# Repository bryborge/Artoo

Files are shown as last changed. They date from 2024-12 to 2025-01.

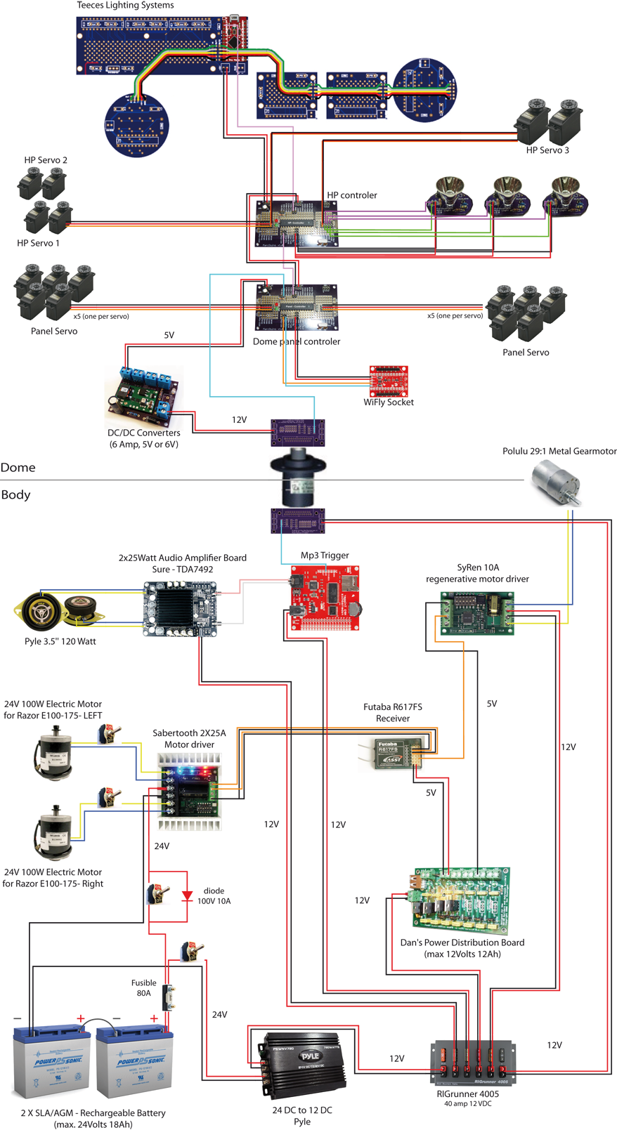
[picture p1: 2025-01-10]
ref/electronics/electronic-schema-24v.png

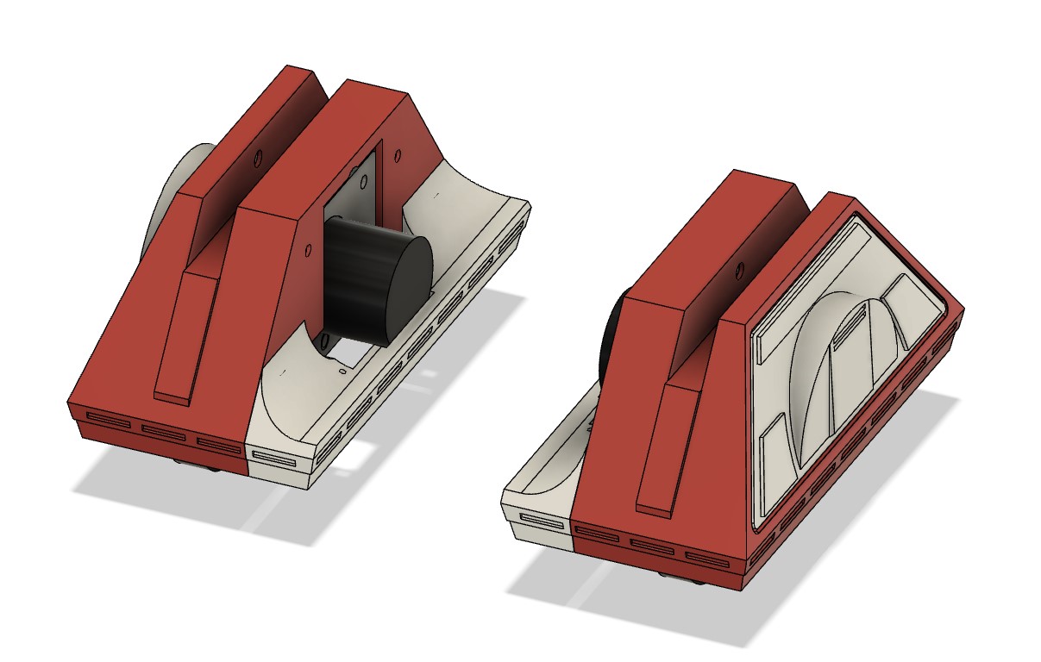
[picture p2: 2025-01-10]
ref/guides/scavenger-drives/Scavenger Drive Foot Covers/Screenshot 2021-05-20 181121.jpg

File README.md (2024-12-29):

# Artoo (Detoo)

Resources, code/sketches, and documentation related to building the Astromech droid R2D2.

## References

### MACs

*   **BT module:** `E8:9C:25:5C:9B:C9`
*   **Foot Controller:** `04:76:6E:85:17:FD`
*   **Dome Controller:** `00:06:F5:B4:F1:E1`

### Further Reading

*   https://github.com/Eebel/SHADOW_MD_EEBEL/blob/master/Shadow_MD_Eebel_Tabbed/a_INIT.ino
*   https://github.com/theFPVgeek/SHADOW/blob/master/Shadow.ino
*   https://www.printed-droid.com/kb/pairing-ps-move-controllers/

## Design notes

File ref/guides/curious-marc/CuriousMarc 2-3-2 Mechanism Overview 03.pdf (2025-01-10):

## “CuriousMarc” 2-3-2 R2-D2 System Overview

Marc Verdiell
Feb. 21, 2011

Foreword
The R2-D2 robot seen in the Star Wars movies has three legs. The legs are in supposedly articulated: the center leg is retractable in the body, while the two outer legs have the ability to pivot around their shoulder articulation.

Thus the robot can be seen in two configurations. In “2-leg” mode, he is standing straight up on its two outer legs with the center leg retracted in the body. In “3-leg” rolling configuration, the center leg is extended and the two back legs are tilted backwards (see Figure 1). In the amateur robot building community, the “2-3-2 capability” refers to the ability of the robot to transition from the 2 legs posture to the 3 legs configuration and back.

The original robots seen in the Star War series actually lacked this capability. In the earlier three Star Wars movies (Episodes IV to VI), where R2-D2 is always an actual robot (in the later movies, he is either an actual robot or a computer graphic generated one), different robots are used for each configuration. The “2-leg” robot is usually not moving, and has space inside for a dwarf actor (Kenny Baker¹

) to sit in and bring him to life by moving the dome and shaking it. You can actually spot two small leg tubes under the body where the dwarf actor can slip his feet.

The 3-legged robots, of which many versions were used, were remote controlled units with fixed legs configuration, the center leg being in fixed extended position and the outer one always leaning back at a fixed 36° angle.

Only one version of the robot, the “pneumatic R2”, had the ability to switch from 2 legs to 3 legs, but not the reverse. This was accomplished by powerful pneumatic actuators. This transition is first seen in a short scene²

of the movie “A New Hope” (Episode IV).

- 1 -

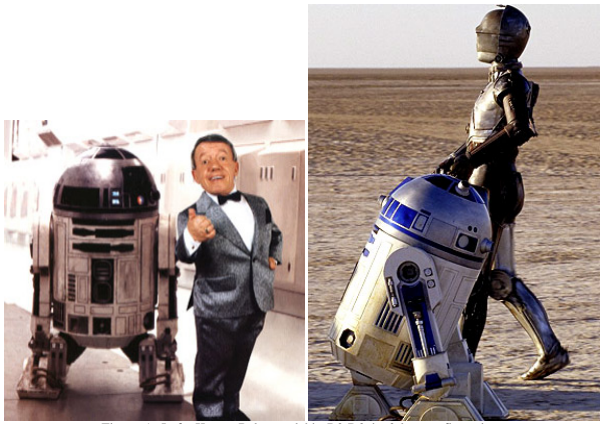
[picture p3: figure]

Figure 1: Left: Kenny Baker and his R2-D2 in 2-leg configuration. Note the tube extensions connecting the underside of the body to the foot shells for the actor’s feet. Right: R2-D2 rolling around in his familiar 3-leg configuration.

Therefore, building an actual 2-3-2 enabled R2-D2 replica goes beyond what the actual movie robots could do, and is generally known as a challenging task for the amateur builder. The difficulties arise not from one particular constraint, but rather from the combination of several of them:
- the limited space available inside the robot, particularly when taking into account the space needed for batteries to operate the robot for long sessions.
- the relatively swift motion necessary to imitate the lifelike 2-3 transition seen in the movie
- the large static and even larger impact forces that the legs and mechanism have to survive once rolling
- synchronizing the movement of the center and outer legs while keeping the robot in balance during the 2-3 and 3-2 transition.
- limited amateur budgets.

Despite these hurdles, several builders have succeeded in building 2-3-2 enabled robots 3, , , , , , , , 4 5 6 7 8 9 10 11. A good discussion of the different approaches used can be found on our builder’s community web forum at astromech.net¹².

- 2 -

This document was put together at the request of one of us (Blake Mann), encouraging all 2-3-2 builders to document their designs to help guiding other builders. It summarizes my own approach to the problem, which owes much to the other builders referenced above. The step by step building progress of my 2-3-2 droid, along with many videos and pictures, is also chronicled on my builder’s log on astromech.net¹³, where I post under my forum moniker “CuriousMarc”.

Shoulder Actuation Mechanism

Figure 2 is a diagram of R2 in 2-leg and 3-leg position. When not standing upright, the angle between the center leg and the outer legs is 36°, which is the amount the shoulder flange on which the outer leg is attached should be rotated by the mechanism.

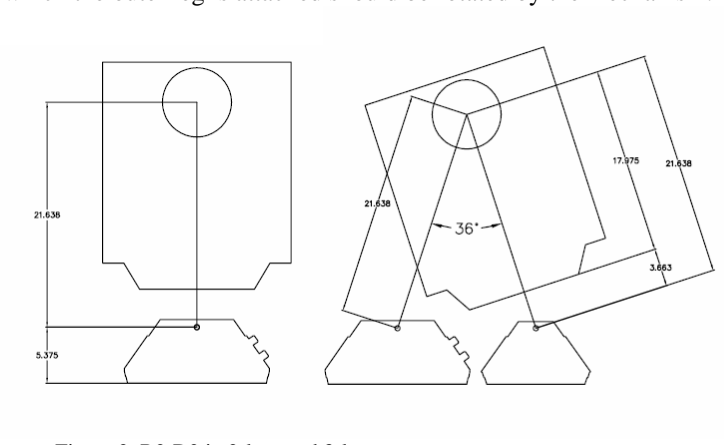
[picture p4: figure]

Figure 2: R2-D2 in 2-legs and 3-legs posture

My shoulder actuation mechanism is shown in Figure 3. It uses a linear actuator instead of the more commonly used, but bulky and fragile, satellite motor arrangement (the “satellite motors” owe their name to their original function, which was to rotate satellite TV dishes).

- 3 -

Figure 3: Views of CuriousMarc’s R2-D2 shoulder actuation mechanism

My R2 is based on the COM-8 frame, made by James Van Reenen (see Figure 4). My COM-8 Frame model is a modified version of the JAG 5 frame originally developed by Jerry Greene. The COM-8 plans are not publicly available, but the dimensions follow the Jerry Greene plans very closely, which are available on his web site 14. I adapted my mechanism to fit the existing frame with little or no modifications. Indeed, one need to drill only two ¼” holes in the COM-8 shoulder plate to accommodate my shoulder mechanism.

- 4 -

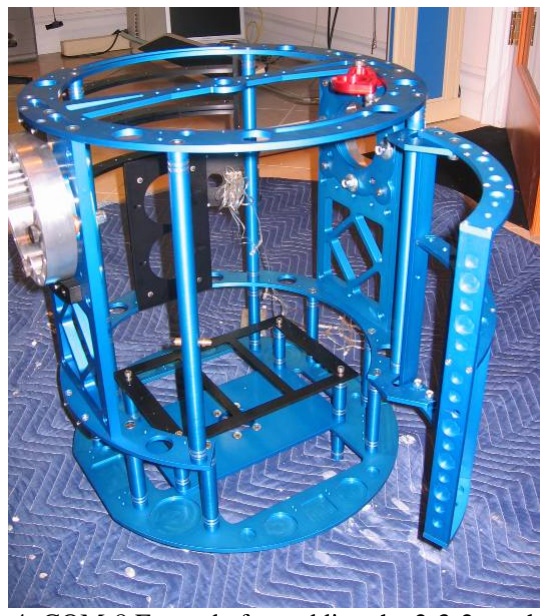
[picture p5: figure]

Figure 4: COM-8 Frame before adding the 2-3-2 mechanism.

The COM-8 shoulder mounting plate is shown in Figure 5. Like the one on the JAG-5 frame, it incorporates 4 curved races that allow for the shoulder flange to rotate through the necessary range. The frame also comes with bronze bushings that slide into the curved openings, so a fair amount of 2-3-2 readiness is already built into the frame.

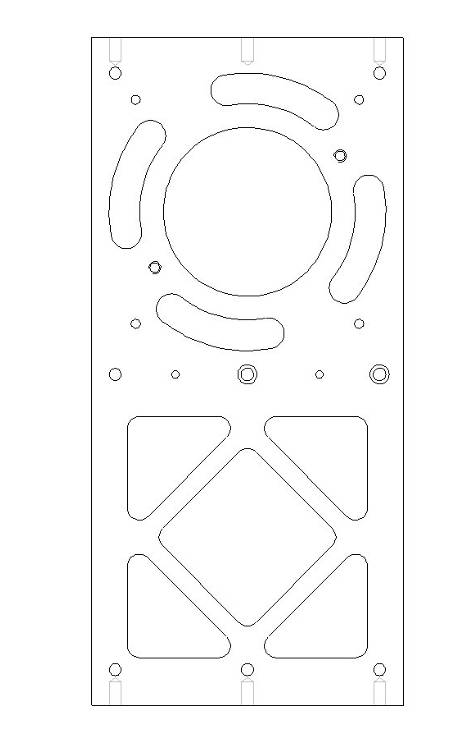
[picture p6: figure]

Figure 5: Shoulder mounting plate that comes with the COM-8 frame, showing the 4 curved 48°openings.

The actual races allow for 48° of movement, 38° in the backward direction (2° more than needed for 3-leg position) and an extra 10° forward, so R2 can actually look down when

- 5 -standing in 2-leg position. My mechanism supports the full range of motion, both backward and forward.

The first task was to size the actuator. Initial calculations showed that two 100 lbs actuator with a 3” stroke would easily cope with a 150 lbs robot, 48° rotation, and a 1 to 2s rotation time using a relatively short lever arm compatible with the available physical space around the shoulder. I chose a 100 lbs semi-custom unit from Motion System¹⁵, model 85615 16 (see Figure 6). This unit has several advantages. It is very compact and fits behind the shoulder plate, is available in 12V drive, has very fast movement (available either 1”/s or 2”/s, I used the slower 1”/s model). Most importantly, it has a recirculating ball screw which allows it to free-wheel at both travel ends, eliminating the risk of mechanical damage.

There are a boat load of options that need to be specified when ordering the actuators, and the final part numbers are 85615-LH-15-3-SBC-0.250-DC1-RE-CT and 85615-RH-15-3-SBC-0.250-DC1-RE-CT. They also became more prosaically known as the “85615 R2-D2” RH and LH actuators (units are not symmetric, you need a right handed and left handed one), I suspect you can re-order them using that simplified code.

The actuator connects at the bottom with a small anchor that I machined, and at the top to a J-bar, as shown on Figure 7. The J-bar connects to the original COM-8 shoulder screws, with the simple addition of slippery Rulon and Nylon thrust washers sandwiched between the bar and the shoulder plate. The J-bar dimensions are given in Figure 8, and are intended to give full 48° range of motion with a 3.0” stroke from the actuator.

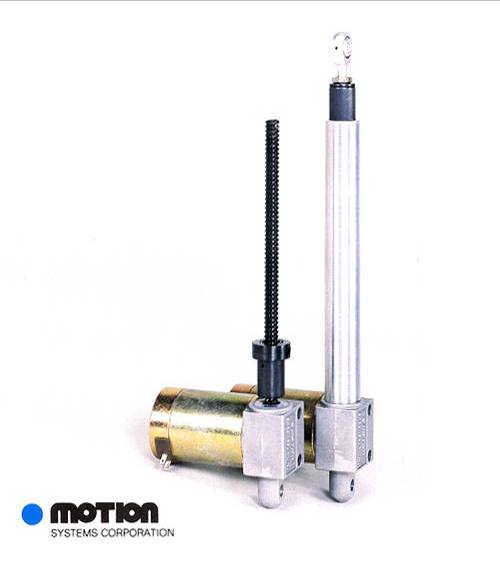
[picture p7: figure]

Figure 6: Linear Ball Drive Actuator model 85615 from Motion System Corp.

- 6 -

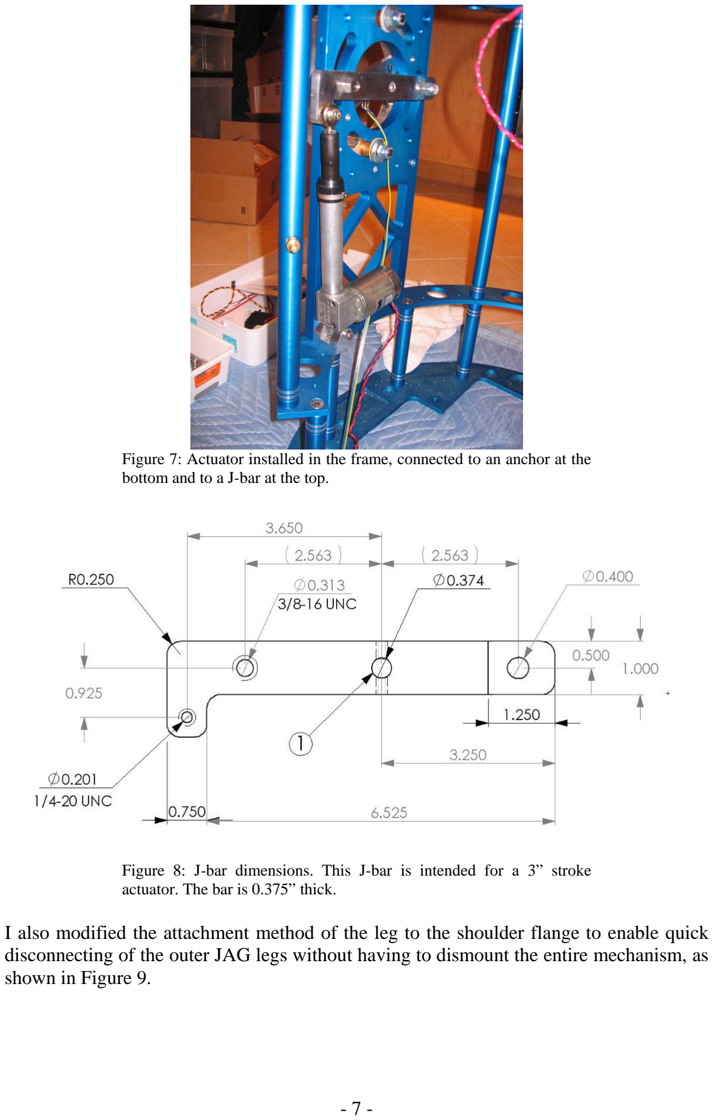
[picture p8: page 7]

Figure 7: Actuator installed in the frame, connected to an anchor at the bottom and to a J-bar at the top.

Figure 8: J-bar dimensions. This J-bar is intended for a 3” stroke actuator. The bar is 0.375” thick.

I also modified the attachment method of the leg to the shoulder flange to enable quick disconnecting of the outer JAG legs without having to dismount the entire mechanism, as shown in Figure 9.

- 7 -

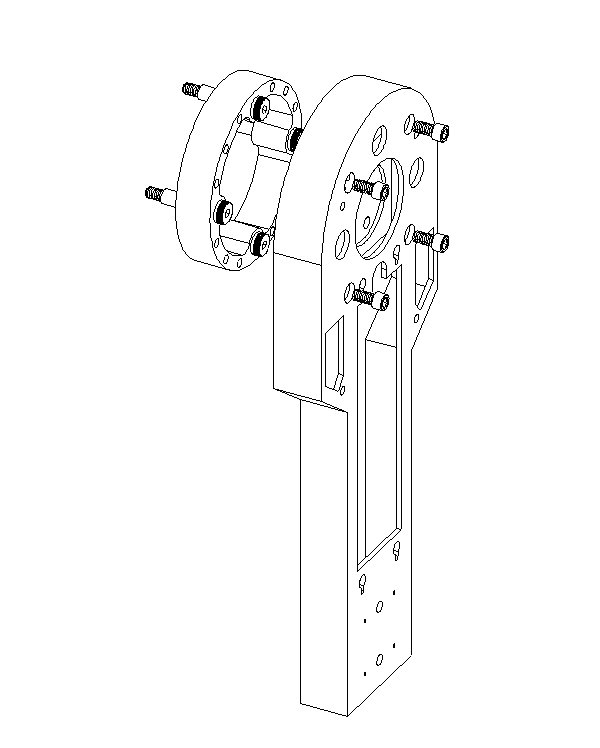
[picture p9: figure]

Figure 9: Modified leg to flange assembly.

Outer Leg servo control

I control the outer leg position in a continuous and analog fashion like a regular servo. I used a linear 10kΩ potentiometer as a position sensor. When connected to a motor controller having feedback capability, this effectively transforms the leg actuator into a giant servo. This way, no limit switches are necessary, and the 2-leg, 3-leg and lookdown positions can be adjusted using the RC transmitter programming, or software in the 2-3-2 motion controller as I describe later on. Also, all intermediate positions of the leg can be accessed.

A spanner was designed to fit inside the shoulder flange opening and hold the position sensing potentiometer, as well as a mounting pin for the ankle angle control bar to be discussed below. The spanner mounts on the outside of the shoulder plate using the two aforementioned ¼” holes drilled in the plate. Drilling these holes is the only modification necessary to the COM-8 hardware. The spanner is shown in Figure 10.

For the servo motor control, I used a RoboteQ AX500 dual 2x15A controller¹⁷. To be fair, this is a bit of an overkill, as the motors do not consume more that 2A and I do not use any of the advanced features. Simpler units from Polulu (use units with position feedback) might be a more economical fit¹⁸.

- 8 -

Figure 10: Spanner with the potentiometer and anchor pin attached (left), spanner mounted on the outside of the shoulder plate (right).

Outer Ankle Locking
One of the trickiest aspect of the 2-3-2 mechanism is the locking of the ankle pivots. The foot shell normally connect to the leg ankle at a pivot point, and is left free to rotate around that articulation. However, the outer ankle-to-foot pivots need to be rigidly locked in 2-leg position so the droid doesn’t fall over. But, in 3-leg mode, the foot shell needs to be at 18° from the horizontal, bisecting the 36° angle of the leg to the body (see Figure 2). Strictly speaking, the outer ankles do not need to be locked at a specific angle in 3-leg position and could be left free. However, builders prefer the added stability and traction provided by locked ankles when driving. Also, reverting from free ankles to locked ankles during the 3-2 transition is a tricky balancing and timing business.

I therefore opted for a simple passive ankle control mechanism, which I believe was first documented in the Carr-Hunger droid. In this implementation, the angle between foot and ankle is maintained at exactly half of the angle of the body to leg at all times via a steel rod, mechanically tying the leg-to-shoulder angle to the foot-to-leg angle.

A few pictures should clarify how this works. A narrow steel bar extends through the whole length of the leg as seen in Figure 11. It goes through a small opening at the bottom of the ankle and is tied to an anchor screw in the foot shell near the pivot point, as shown in Figure 12. The top of the tie rod is attached to a pin near the shoulder pivot point (Figure 13). I have used both stock steel pins (the one in Figure 10) and machined brass pins (see close up in Figure 14) with equally good results. The steel pin is easy to procure, but needs to be force fitted into the spanner, while the machined pin is simply screwed in, but you need to machine it. Choose your own evil…

The trick to maintaining the correct half-angle relationship is to locate the tie point in the foot twice as far from the pivot point as the tie point at the shoulder. In my case, the shoulder pin is ¾” from the center of rotation of the shoulder, while the foot shell tying screw is 1½” from the ankle pivot point, satisfying the needed geometric relationship.

- 9 -

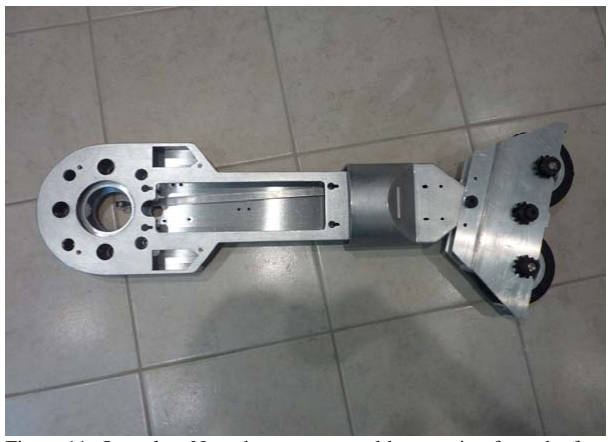
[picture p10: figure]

Figure 11: Outer leg. Note the narrow steel bar running from the foot to the shoulder opening and used for foot angle locking.

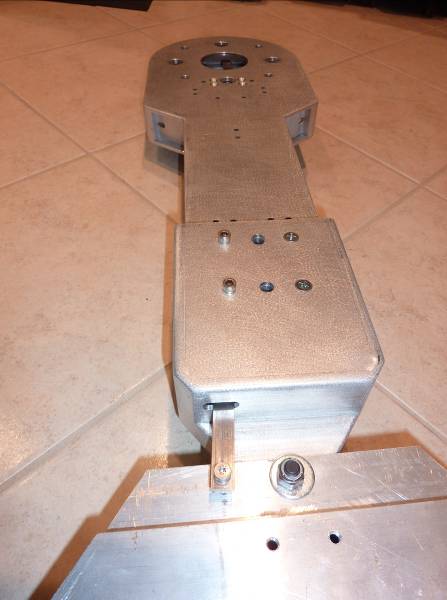
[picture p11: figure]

Figure 12: Lower portion of the outer leg. The ankle tie rod goes through a small opening at the bottom of the ankle and is attached to an anchor screw on the foot shell.

- 10 -

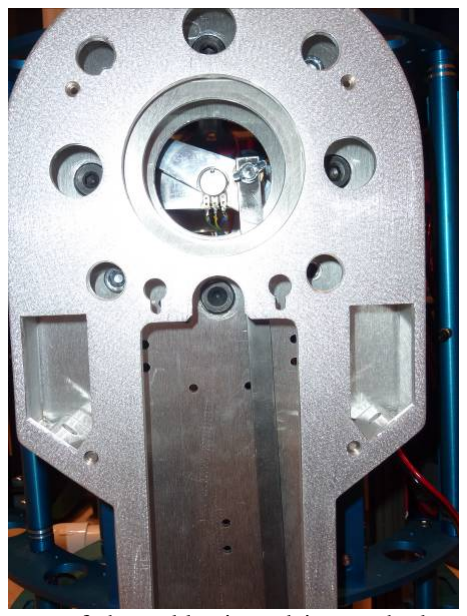
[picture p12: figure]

Figure 13: The top of the ankle tie rod is attached to a pin near the shoulder center of rotation.

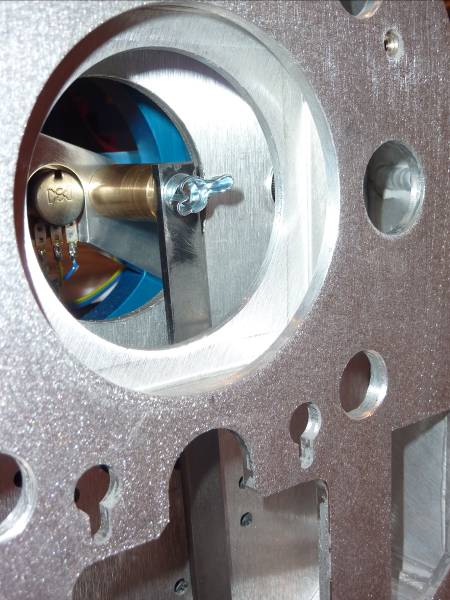
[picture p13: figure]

Figure 14: Detail of the top attachment pin for the tie rod.
Center Leg Lift Mechanism
The center leg lift mechanism was a real head scratcher. One of the best fully documented mechanism I had seen was Mike Lambert’s foot lift, whose plans are available on the Yahoo R2-builders group file section 19. However I did not like the space it consumed at the top of the droid, nor the speed at which it operated. I wanted my foot to drop in a second or two to be more lifelike.

Problem is, when the foot is retracted in the droid body, there is very little space left for a mechanism except towards the top of the body. The mechanism needs a relatively long stroke of 10”. And it has to be extra strong because the center leg has to survive shock

- 11 -impacts many times the weight of the droid from a sudden impact on the front wheels while driving and, unlike the outer legs, these strong forces are right in line with the movement one wants to achieve. Which means such mechanisms are usually large and slow.

After trying many zany configurations that either didn’t provide the speed, the necessary travel length, the strength or the space savings, I finally arrived at a workable solution shown in Figure 15. This self-contained mechanism is also designed to fit into the COM-8 frame with very little modifications, needing just 3 pairs of extra holes on the bottom ring to attach the support brackets.

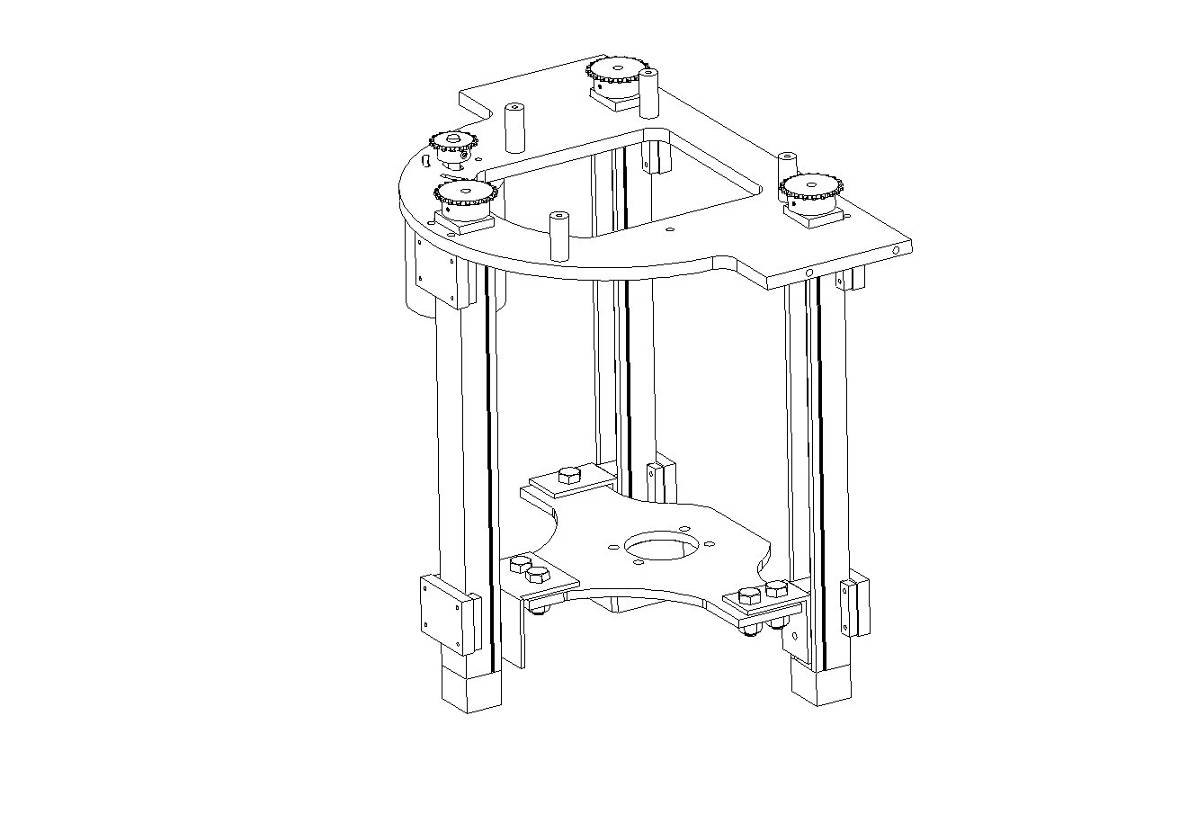
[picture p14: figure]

Figure 15: Center leg lift mechanism

Three screw-actuated linear slides assemblies are the key of the design. The ones I use are manufactured by PBC Linear²⁰. These extruded aluminum units are relatively low cost actuators (that is, relative to most professional linear motion equipment!), very compact, yet have enough structural strength for our application. They can be ordered semi-custom in any length, with several choices of screw pitch. A shown in Figure 16, they are relatively simple units. A slider moves along in an extruded aluminum shell when turning the lead screw. The exact part number for the PBC slide is MLD028D-0AJ201-0338-000 (28x338 mm actuator, 10 mm lead screw).

- 12 -

Figure 16: PCB Linear MLD actuator, part number MLD028D-0AJ201-0338-000. It has a 338mm main body length and a 10 mm lead screw.

One would be tempted to use only one of these slides. However, although they are acceptable (while not spectacular) in axial load performance, they are pretty poor in moment load. They would fail if a large force would tend to twist and rotate the slider. Unfortunately there would be plenty of that if only one of the units was attached to a side of the platform holding the leg. To go around that problem, I use three slides attached around the moving platform. They are all driven in unison by a chain and sprocket system, so that the platform always stays flat and no large moment force can ever develop. A quick calculation showed that the load of a 150 lbs robot including impact load was acceptable, albeit without much margin. Drive carefully as they say.

Next was the issue of travel. A full 10” of travel is needed to barely fit the leg inside the body. Add 0.30” of margin for over-travel at either end, the slider length and the length of the end cap of the units, and quite miraculously the unit barely fits inside the body without going above shoulder level. Beware that the slides protrude all the way down into the skirt, so resin skirts with thick solid sides are out.

Finally, there was the issue of torque and speed. Given the maximum 3,000 rpm critical speed of the screw, there are several combinations of lead screw pitch and drive speed that can achieve the desired 10”/s speed. I chose a 10mm lead screw, which yields a 1500 rpm actuation for the 10”/s speed goal. This would allow up to 2:1 gear reduction to increase torque from typical brushed electrical motors that run in the 2000-3000 rpm regime. Assuming this reduction and a 15 lbs leg weight, calculations showed that a motor with at least 50 oz/in torque and 40W would be needed. A cheap surplus 100W, 12V, 2500 rpm (no load) scooter motor fits the bill with good margin and is small enough to fit underneath the mechanism. The final gear ratio I used was 15 teeth on the motor and 20 teeth on the actuators. I used a #25 chain. The scooter motor has no trouble at all with my heavy center foot and achieved the calculated speed. My only complaint is that it is a bit noisy.

Figure 17 shows the parts needed to assemble the leg lift. They are the top platform and the sliding plate, and a bunch of mounting brackets. They would probably be difficult to replicate without having some machining tools, but could easily be made in a machine shop run. Figure 18 and Figure 19 show the completed assembly in the droid frame.

- 13 -

Pictures do not do much justice to the “life” a quick leg drop brings to the transition, however you can get a better idea from a YouTube video I posted at http://www.youtube.com/watch?v=v9vhstzh6Ok , which is also available along with a few more in my build log.

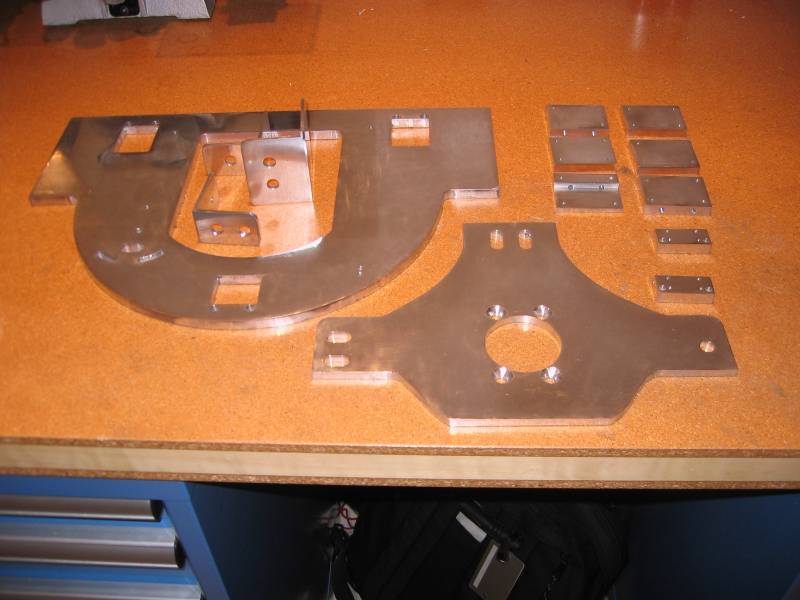
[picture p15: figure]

Figure 17: Aluminum pieces needed for the leg lift.

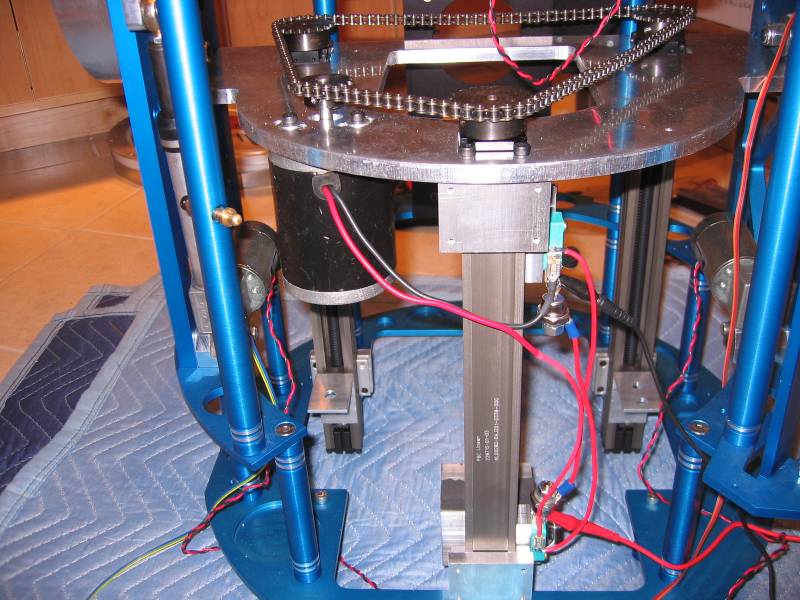
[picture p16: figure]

Figure 18: View of the leg lift mechanism during assembly.

- 14 -

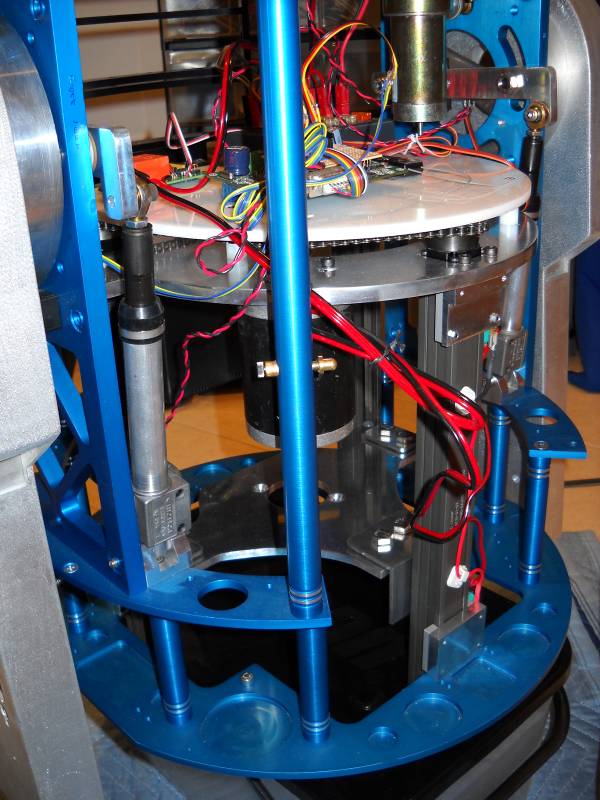
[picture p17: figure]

Figure 19: Completed Leg Lift mechanism.

Center Foot servo control
I used a simple RC dual relay board to actuate the center foot up or down from and RC signal. I bought mine from robotmarketplace.com²¹ (Figure 20). The end travel is controlled by simple micro-switches in either direction, shunted by power diodes to allow reverse movement once the end travel is reached. One could also use a RC brush motor controller and gain some speed control, and maybe I’ll upgrade to that when I get the time. Just be sure to size your relays or speed controller appropriately, the motor can draw up to 10A at full tilt.

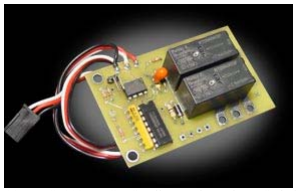
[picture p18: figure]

Figure 20: RCE220 RC Small Dual Relay Switch from robotmarketplace.com

- 15 -

One issue I had with the simple limit switch setup is that since the leg moves very fast and is heavy, cutting the motor supply was not enough to stop the movement. The assembly would travel past the limit switches and bump into the mechanical stops at both ends. In order to decelerate the foot more efficiently at the end of travel, I also use the motor as an electric brake by shunting it. I was able to accomplish this automatically by adding two more (powerful!) shunting diodes to the system as shown schematically in Figure 21.

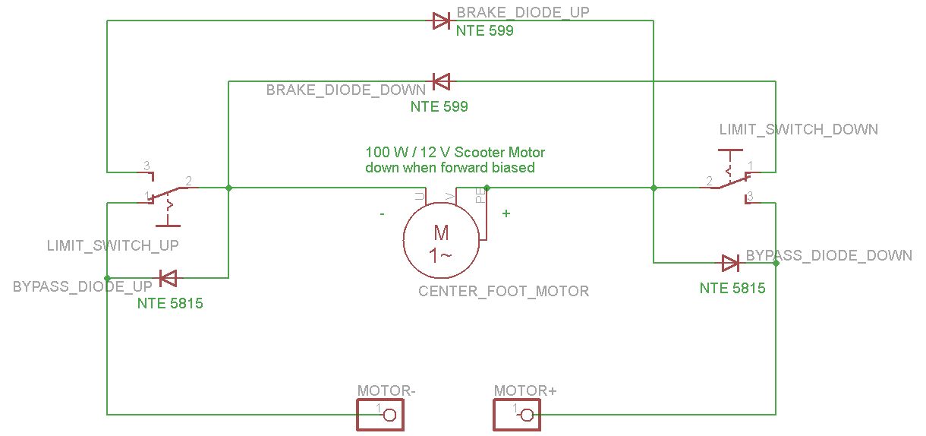
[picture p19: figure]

Figure 21: Limit switches and diodes for the end travel control. The two large NTE599 15A cont / 250A max diodes are for braking at travel end.

The diodes have to be of the larger kind, I use NTE5815 (Io 6A, Imax 400A) over the end switches and two NTE955 (Io 15A, Imax 250A) on a heatsink as the breaking diodes.

Center Foot considerations

I used a two caster setup for my center foot. By using two casters, the center ankle articulation is left unlocked, and the foot naturally adjust to the required angle, which continually varies during the 2-3-2 transitions. The largest caster I could fit is a 3” caster from Mitsumi²². Another builder (TinyP²³) discovered them, they are the only ones whose swivel radius is small enough for two casters to fit in the foot shell without interfering with each other or with the shell skirt when turning around.

One must be careful to introduce some kind of shock absorption device between the actuation mechanism and the center foot wheels, or all shocks would be transmitted directly to the screw actuators. The heavy Mitsumi steel casters are designed for very heavy loads (which is probably why the swivel radius was kept so small), and therefore come with very hard wheels. To provide some shock absorption, I replaced the wheels with soft neoprene wheel from another 3” caster (Figure 22). To provide further shock

- 16 -absorption, I added rubber absorbers (vibration mounts) between the caster plate and the foot shell (Figure 23).

Figure 22: Misumi casters, with the original hard wheel at right, and grafted with a soft neoprene wheel at left

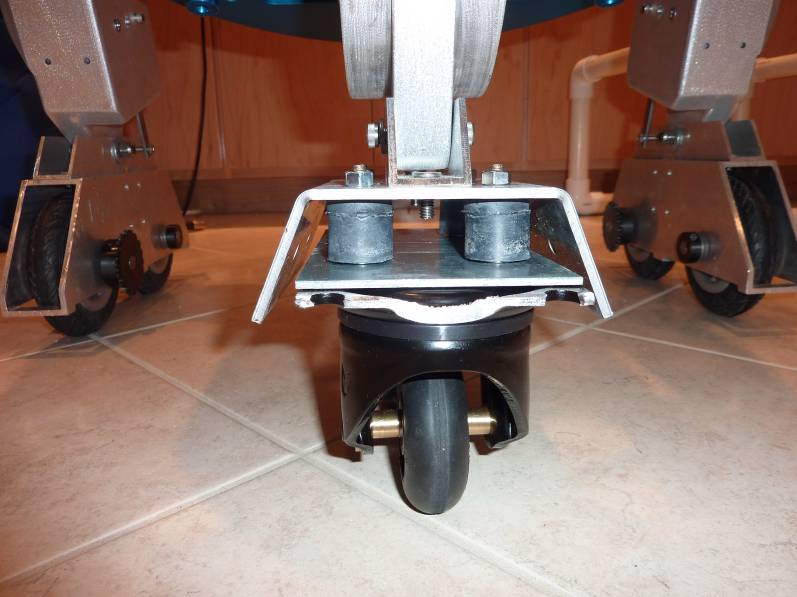
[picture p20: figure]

Figure 23: Rubber mounts are inserted between the caster place and the foot shell for shock absorption.

2-3-2 Motion Controller
With the simple system described above, I was able to do manual 2-3-2 transitions right from my RC controller without further ado. I controlled the outer leg servo with my flap lever, and the center leg via a 3 position switch. However, one has to be careful to first
- 17 -lower the center leg, then move the legs – and the reverse for the 3-2 transition. Do that in the wrong order and the droid will do the dreaded “face plant”.

Most 2-3-2 builders add some form of a controller to synchronize the outer leg and center foot movements for the transitions. I chose to implement this function via a microcontroller, which I can program to output the correct servo signals to feed my three leg servo controllers (two outer legs proportional servo control, and the center leg up/off/down control). It’s a significant programming investment to implement it, but once it’s done it becomes extremely flexible, since all optimizations can be done via software.

The basic system architecture is shown in Figure 24. The microcontroller reads 3 channels from the RC receiver (outer leg channel, center leg channel, and failsafe channel) and 1 analog channel (position sensor of the left outer leg). It outputs 3 servo channels, one for each outer leg and one for the center leg.

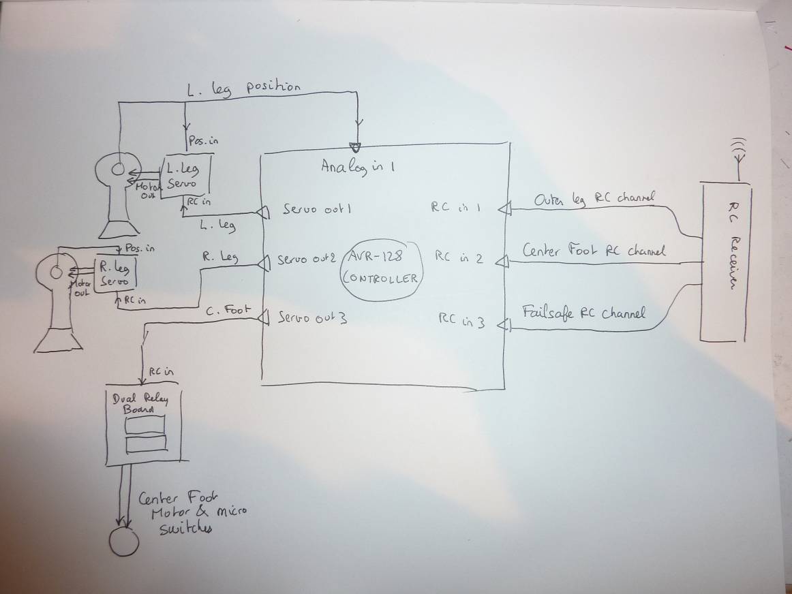
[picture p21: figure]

Figure 24: 2-3-2 control architecture

I used a small and inexpensive Olimex development board powered by an 8-bit Atmel AVR ATmega128 microcontroller²⁴ depicted in Figure 25. In essence it’s very much like an Arduino with a small keypad and LCD screen and a more powerful processor. The amount of microcontroller hardware you get nowadays for about $50 is just downright mind-boggling. This little controller has a 16 MIPS RISC processor, EEPROM, RAM, Flash Memory, 4 independent timers, a real time clock, two independent serial interfaces with support for RS232 and I2C, a whole bunch of PWM generators, 53 pins

- 18 -programmable for input or output, 8 ADC inputs, 8 external interrupts, brownout protection, 6 sleep modes, a bootloader section, in-situ programming, JTAG debug… The list just goes on and on, and so does the 386 pages long manual! And, let’s not forget, unlike PC processors, power consumption is just about negligible. It’s a robot maker paradise or hell, depending on your love of hard core C programming.

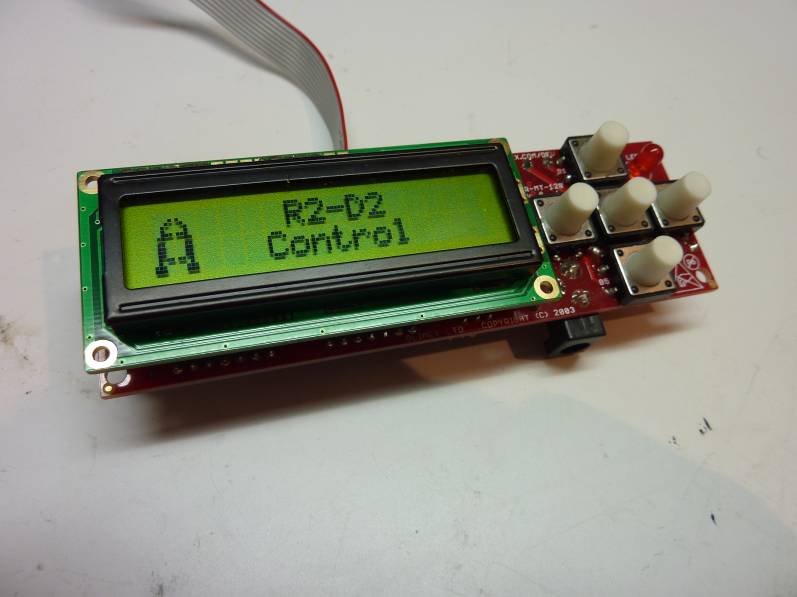
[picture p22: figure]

Figure 25: Olimex AVR-MT-128 microcontoller board

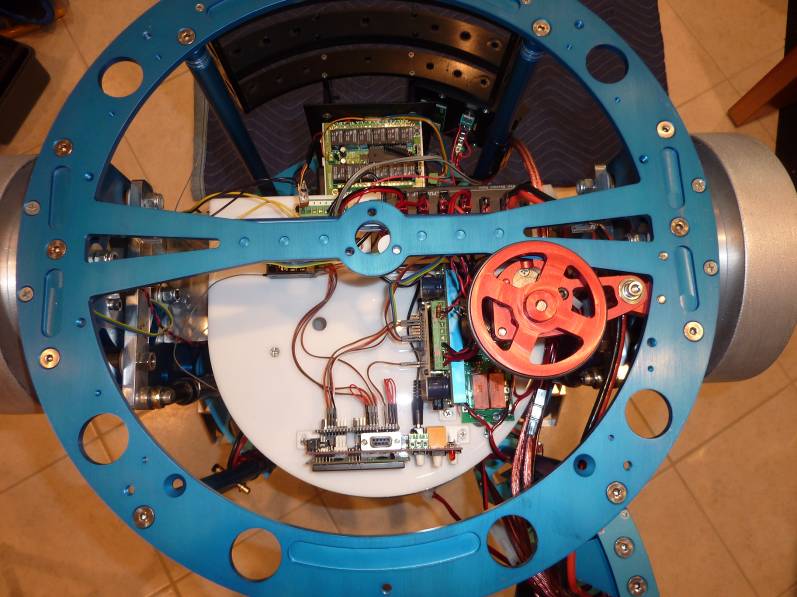
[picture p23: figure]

Figure 26: View of the installed electronics. Controller is at the bottom, to the right is the outer leg servo controller. The relay board for the center foot is partially visible under the dome wheel.

- 19 -

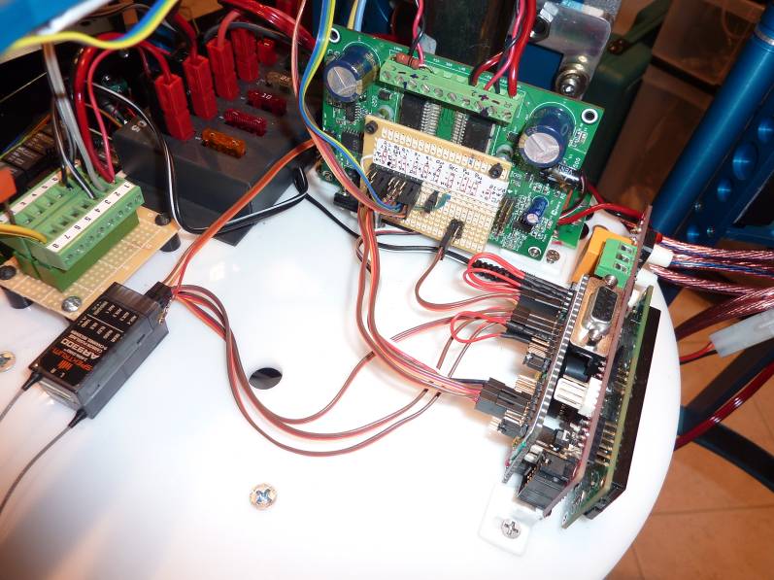
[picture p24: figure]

Figure 27: Close-up view of the electronics. RC receiver to the left, outer leg servo controller to the top, microcontroller to the right.

Figure 28: Controller display in auto mode. The outer legs have been commanded in 2-leg position, as indicated by the close to 500 µs leg channel value read from the RC transmitter. Accordingly, the center leg has been brought to up (U) position. A cumulative run-time counter is at the lower left – R2 has been up for less than a minute and still shows 00:00.

In regular auto mode, the controller simply monitors the outer leg lever position from the RC transmitter. Starting from 2-position, the first little bit of lever position does nothing, then past a certain point the center leg deploys, and the outer leg follows the position of the lever. The outer legs can be moved all the way to full back 3-leg position, or can be brought to any intermediary position using the lever. If the controller senses that the outer legs are brought back all the way upright to 2-leg position, it automatically raises the

- 20 -center leg. While this happens, some basic info is available on the LCD screen for monitoring (Figure 28).

Note that for safety, the controller also monitors an extra “failsafe” channel. If this channel has no signal, goes into a predetermined failsafe state due to a loss of signal at the receiver, or is manually set by a switch on the RC transmitter, all 2-3-2 leg movement is disabled.

In addition to the auto mode, the controller also supports a direct RC mode, a manual mode, a calibration mode and a diagnostic mode. In RC mode, the controller simply passes the RC signals from the transmitter to the outer and center leg, in essence reverting back to my earlier manual control setup. In manual mode, legs can be activated locally at the robot using the controller keypad. The calibration mode is used to set the 2 leg and 3 leg position, even out the two outer legs via software in case there is a small angular difference between them, and set the points at which the 2-3 and 3-2 transitions occurs. Finally, in diagnostic mode, numerical values read for each RC channel (I can read up to 6 of them), each servo output value (also 6), and each analog input (4 of them) are displayed for diagnostic purposes.
Power system
Even with a relatively compact system, battery space is quite limited in a 2-3-2. To save space and weight, I have been using Lithium-Polymer batteries instead of the standard lead-acid ones. The Lithium-Polymer units have 5 times the energy density of lead-acid batteries. I used three 10Ah/14.8V packs²⁵ connected in parallel, for an equivalent capacity of 30 Ah. The batteries are small enough to fit in the back door (Figure 29).

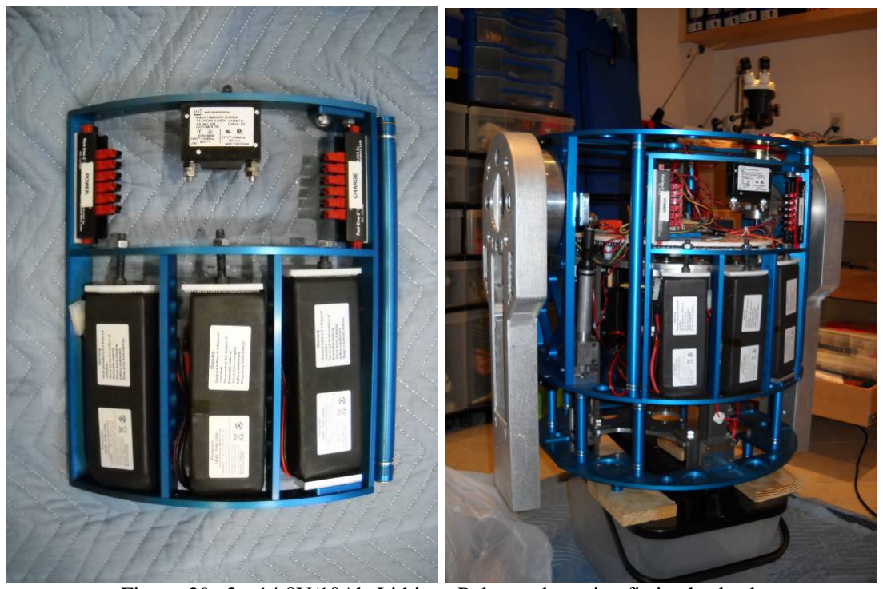
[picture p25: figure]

Figure 29: 3x 14.8V/10Ah Lithium Polymer batteries fit in the back door.

- 21 -

However in actual use I found that the droid was balanced too far to the back – which helps the 2-3 transition, but unfortunately makes driving on 2 legs a bit iffy. The droid would be susceptible to falling backwards when accelerating. I therefore later moved one of the batteries to the front for balance. Fortunately they are so small that you can fit them pretty much anywhere.
Closing Remarks
Figure 30 shows the finished installation. Completion of my 2-3-2 system is recent, so I do not have much extended data on actual use, but it has performed well right from the get go.

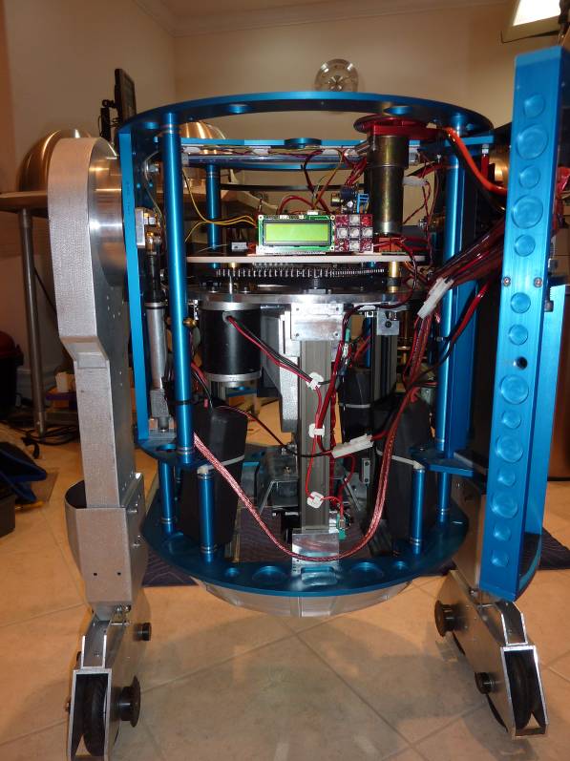
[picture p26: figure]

Figure 30: Finished 2-3-2 installation. Note the batteries in temporary position for balance trials. Eventually I settled on two batteries in the back door and one in the front.

There are a few things I’d change if I was going to make revision 2. The 10mm pitch screw for the center foot elevator is probably a bit too much. The center leg has a slight tendency to retract under the weight of the robot. I eliminated that by introducing a little bit of friction with a belt on the side of the motor shaft, but this is an afterthought kludge in an otherwise clean design. If I had to redo it, I would probably use a 5mm screw instead and compensate for speed with less of a gear reduction.

It is also conservatively designed and expensive. To cost reduce version 2, I would use only one shoulder actuator instead of two, and simply connect the two legs via the classic gas pipe. It would save one actuator and one motor controller cost. Also, now that the three screw system has been proven to work, I would not use pre-made slide assemblies

- 22 -whose precision widely exceeds what we actually need. Instead I would just use regular lead screws, nuts and a few ball bearings and build them into my own mechanism.

Another thing one could do is lighten the frame. Everything gets simpler and more reliable when weight is lower. Since all the weight of the center leg is now transmitted to the top plate of the center foot lift mechanism, the frame itself really does not have to support any weight. Also the horizontal plate greatly reinforces the frame, as do the three vertical slide units. I have effectively built a stronger inner frame inside the original frame. Consequently, the original frame, which is quite heavy, does not need to provide much structural strength anymore. It could be made much lighter without compromising the robot structural integrity.

We have reached the conclusion of this article, however we are at page 23 of what is after all just a quick overview. This should serve as a stern reminder of the significant complexity and challenges that a 2-3-2 system adds to a build. It can be done, and I hope this write-up encourages other builders to take the plunge, but it is definitely not for the faint of heart nor the faint of budget.

- 23 -

References

1
Kenny Baker’s bio: http://en.wikipedia.org/wiki/Kenny_Baker

2
2-3 transition clip from the original movie: http://www.mikeverta.com/Posts/2-3-2.mov

3 Carr-Hunger 2-3-2: http://www.alexkung1.com/r2d2/47/page_01.htm

4
Craig Smith 2-3-3 video: http://www.youtube.com/user/bomarmonk#p/u/9/dSCcJg1n93Y

5
Rob Meyer's 2-3-2 build thread: http://astromech.net/forums/showthre...ght=successful (http://astromech.net/forums/showthread.php?t=2742&highlight=successful)

6 Blake Mann linear actuator demo
http://astromechbuilder.com/mechload...uator.MPG.html (http://astromechbuilder.com/mechloader/v/BMann/2-3-2+linear+actuator/Linear+Actuator.MPG.html)

7
Bob Ross 2-3-2 video at Celebration V: http://www.youtube.com/watch?v=zDn9FnT6buo

8 Cory Paccione 2-3-2 video http://www.youtube.com/watch?v=UBhOSHtnBtQ&NR=1

9 Jedineo 2-3-2 http://astromech.net/?q=gallery&g2_itemId=30461

10 Alex Chamberlain 2-3-2 build log: http://astromech.net/forums/showthread.php?t=5172

11 Olivier Lanvin 2-3-2 build log http://translate.googleusercontent.c...9MMttoJGOtjbYQ (http://translate.googleusercontent.com/translate_c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)

12 How many droids ACTUALLY 2-3-2? http://astromech.net/forums/showthread.php?t=1543

13 CuriousMarc 2-3-2 build log: http://astromech.net/forums/showthread.php?t=2957

14 Jerry Greene’s JAG 5 Frame drawings: http://r2-r9.com/Gallery_Drawings.html

15 Motion System Corporation, 600 Industrial Way West, Eatontown, New Jersey 07724 USA Tel. (732) 222-1800., http://www.motionsystem.com .

16 100 lbs linear actuator model 85615: http://www.motionsystem.com/85615/85615-0.htm

17 RoboteQ AX500 controller: http://www.roboteq.com/brushed-dc-motor-controllers/ax500-low-power-2-x-15a-brushed-dc-motor-controller (http://www.roboteq.com/brushed-dc-motor-controllers/ax500-low-power-2-x-15a-brushed-dc-motor-controller)

18 Polulu motor controllers: http://www.pololu.com/catalog/category/95

19 Mike Lambert center leg mechanism: http://movies.groups.yahoo.com/group/r2builders/files/2-3-2/

20 MLD series actuators, PBC Linear, 6402 Rockton Road, Roscoe, IL 61073, Phone: (888) 389-6266. http://www.pbclinear.com/MLD-Series-Linear-Actuator

21 RCE220 RC Dual Relay RC switch from RobotMarketPlace.com: http://www.robotmarketplace.com/products/0-TD-RCE220.html

22 Mitsumi Misumi Heavy Load Caster , part # CSHN75-N, http://us.misumi-ec.com/

23 TinyP astromech post on 3” casters from Mistusmi: http://astromech.net/forums/showpost.php?p=32767&postcount=68

24 Olimex AVR-MT-128 development board: http://www.olimex.com/dev/avr-mt128.html

25 10 Ah, 14.8V Lithium Polymer battery packs from batteryspace.com: http://www.batteryspace.com/highpowerpolymerliionbattery148v10ah148wh30aratewithpcmandfuelguagedisplay.aspx (http://www.batteryspace.com/highpowerpolymerli-ionbattery148v10ah148wh30aratewithpcmandfuelguagedisplay.aspx)

- 24 -

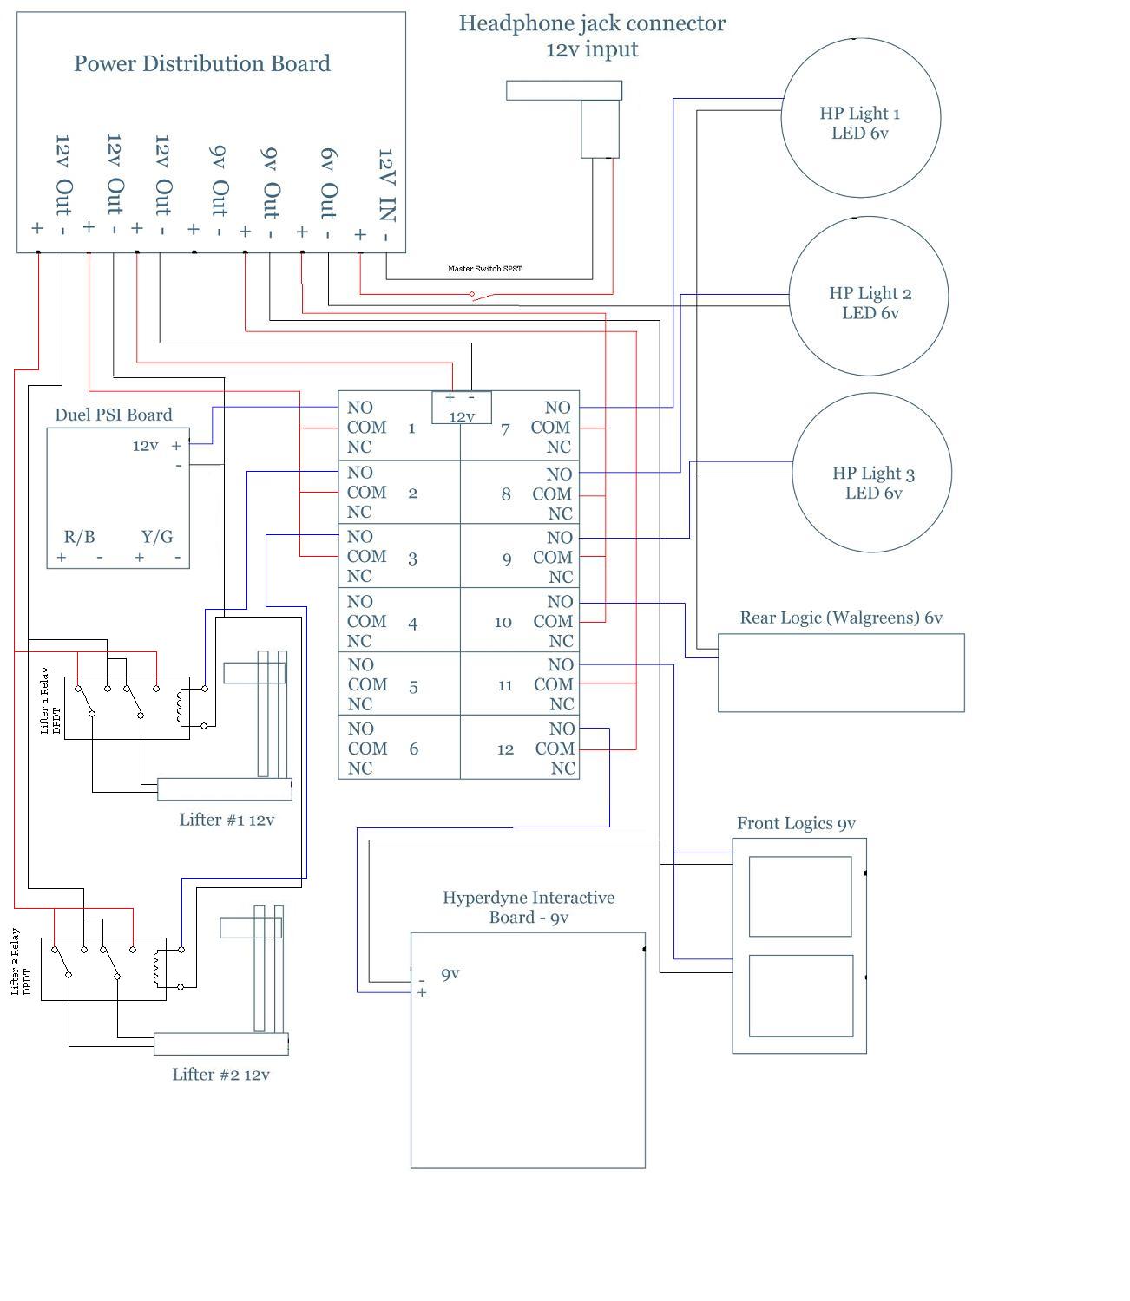
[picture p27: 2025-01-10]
ref/electronics/wiring/R2_Dome_Electronics-jh-version2.JPG

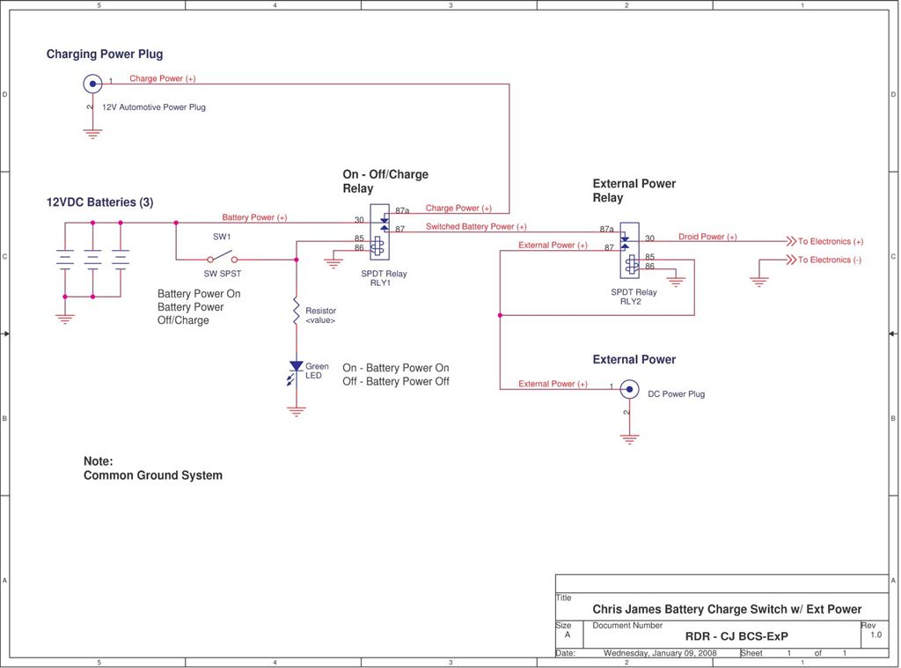
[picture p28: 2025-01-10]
ref/electronics/battery-charging-circuit-diagram.jpg

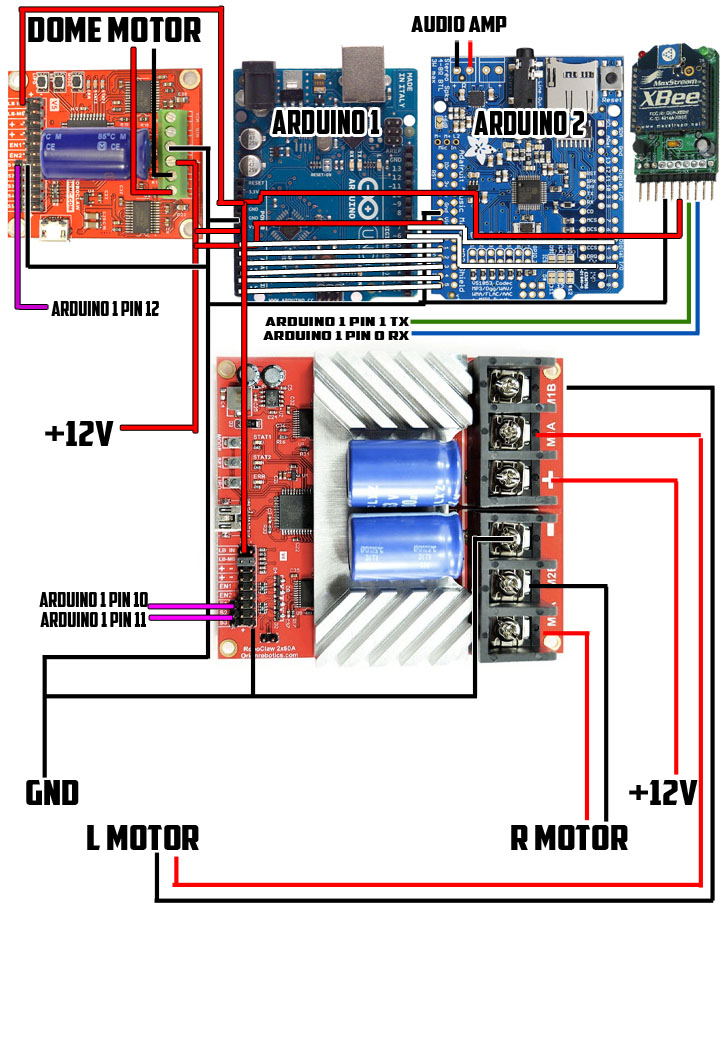
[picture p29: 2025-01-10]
ref/electronics/basic-schema-12v.jpg

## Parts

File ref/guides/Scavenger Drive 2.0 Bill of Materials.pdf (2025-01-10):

# Scavenger Drive 2.0 Bill of Materials

## Aluminum Plates

DXF Files - Cut using Aluminum 5052 .125 Thickness
Ensure you have the latest and greatest DXF files.

Note: the included top bracket where the ankle will attach is currently designed to match up with Baddeley Remixed 3D Printed Foot Shells.

## Drive Parts

Robot Market Place
2 X 4 Inch BattleKit Robot Wheel - 19-Tooth Sprocket (https://www.robotmarketplace.com/products/0-4-19wheel.html)

Vex Robotics
2 X 3.25" Omni-Directional Wheel (https://www.vexrobotics.com/omni-wheels.html)
1 X #35 Roller Chain (10') (https://www.vexrobotics.com/roller-chain.html)

Amazon
2 X AmpFlow E30-150 Brushed Electric Motor, 12V, 24V or 36 VDC, 5600 RPM (https://www.amazon.com/gp/product/B009YJOD56/ref=oh_aui_detailpage_o02_s01?ie=UTF8&psc=1) 2 X Jeremywell #35 Roller Chain Sprocket B Type 1/2" Bore 10 Tooth (https://www.amazon.com/dp/B08DDJZRBF?psc=1&ref=ppx_yo2ov_dt_b_product_details)

Home Depot
4 X 1/2 in. Zinc-Plated Cut Washer (https://www.homedepot.com/p/Everbilt-1-2-in-Zinc-Plated-Cut-Washer-807246/204633084)
14 X 3/8 in.-16 x 3-1/2 in. Zinc Plated Hex Bolt (https://www.homedepot.com/p/Everbilt-3-8-in-16-x-3-1-2-in-Zinc-Plated-Hex-Bolt-800876/204645567)
2 X 3/8 in.-16 Zinc Plated Nylon Lock Nut (10-Pack) (https://www.homedepot.com/p/Everbilt-3-8-in-16-Zinc-Plated-Nylon-Lock-Nut-10-Pack-822592/317479562)
1 X 3/8 in. Stainless Steel Flat Washer (3-Pack) (https://www.homedepot.com/p/Everbilt-3-8-in-Stainless-Steel-Flat-Washer-3-Pack-800361/204276464)

AluminumSpacer.Com Note : the website is wonky sometimes it’s best to check out as a guest or if you have issues contact Brenda.
For those of you who want the spacers converted to mm (https://www.google.com/search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) <----Click Here----
4 X Aluminum Spacer 1/2 OD x .382 ID x 1-1/2 Long (https://www.aluminumspacers.com/spacers-by-hole-size/hole-for-3-8-inch-bolts/as50-18-96)
6 X Aluminum Spacer 1/2 OD x .382 ID x 1.000 Long (https://www.aluminumspacers.com/spacers-by-hole-size/hole-for-3-8-inch-bolts/as50-18-64)
4 X Aluminum Spacer 1/2 OD x .382 ID x 7/16 Long (https://www.aluminumspacers.com/spacers-by-hole-size/hole-for-3-8-inch-bolts/as50-18-28)
6 X Aluminum Spacer 1/2 OD x .382 ID x 13/16 Long (https://www.aluminumspacers.com/spacers-by-hole-size/hole-for-3-8-inch-bolts/as50-18-52) 4 X Aluminum Spacer 1/2 OD x .382 ID x 11/16 Long (https://www.aluminumspacers.com/spacers-by-hole-size/hole-for-3-8-inch-bolts/as50-18-44) 4 X Aluminum Spacer 1/2 OD x .382 ID x 1-3/16 Long (https://www.aluminumspacers.com/spacers-by-hole-size/hole-for-3-8-inch-bolts/as50-18-76) 4 X Aluminum Spacer 3/4 OD x .509 ID x 7/16 Long (https://www.aluminumspacers.com/spacers-by-hole-size/hole-for-1-2-inch-bolts/1-2-id-3-4-od/as75-22-28) 2 X Aluminum Spacer 3/4 OD x .509 ID x 7/32 Long (https://www.aluminumspacers.com/spacers-by-hole-size/hole-for-1-2-inch-bolts/1-2-id-3-4-od/as75-22-14)

McMaster-Carr
Alternate place to Buy Spacers (https://www.mcmaster.com/products/spacers/spacers~/aluminum-unthreaded-spacers/od~1-2-2/od~0-500/od~0-5/id~0-192/)

## Center Foot Parts

Vex Robotics
2 X 1.125" Bearing Pilot Plastic VersaHub (1/4" Wide, w/ Plate Sprocket Mount) (https://www.vexrobotics.com/versahubs.html)
4 X 4" Omni-Directional Wheel v2 (https://www.vexrobotics.com/omni-wheels.html)
4 X 0.500" ID x 1.125" OD x 0.313" WD (Flanged Bearing) • $2.99 SKU#: 217-2731 (https://www.vexrobotics.com/pro-bearings.html)

Home Depot
5 X 3/8 in.-16 x 4-1/2 in. Zinc Plated Hex Bolt (https://www.homedepot.com/p/Everbilt-3-8-in-16-x-4-1-2-in-Zinc-Plated-Hex-Bolt-800896/204645571)

AluminumSpacer.com
4 X Aluminum Spacer 1/2 OD x .382 ID x 3/4 Long (https://www.aluminumspacers.com/spacers-by-hole-size/hole-for-3-8-inch-bolts/as50-18-48) 2 X Aluminum Spacer 1/2 OD x .382 ID x 1-3/8 Long (https://www.aluminumspacers.com/spacers-by-hole-size/hole-for-3-8-inch-bolts/as50-18-88) 2 X Aluminum Spacer 1/2 OD x .382 ID x 1/8 Long (https://www.aluminumspacers.com/spacers-by-hole-size/hole-for-3-8-inch-bolts/as50-18-8) 4X Aluminum Spacer 1/2 OD x .382 ID x 1-1/2 Long (https://www.aluminumspacers.com/spacers-by-hole-size/hole-for-3-8-inch-bolts/as50-18-96)

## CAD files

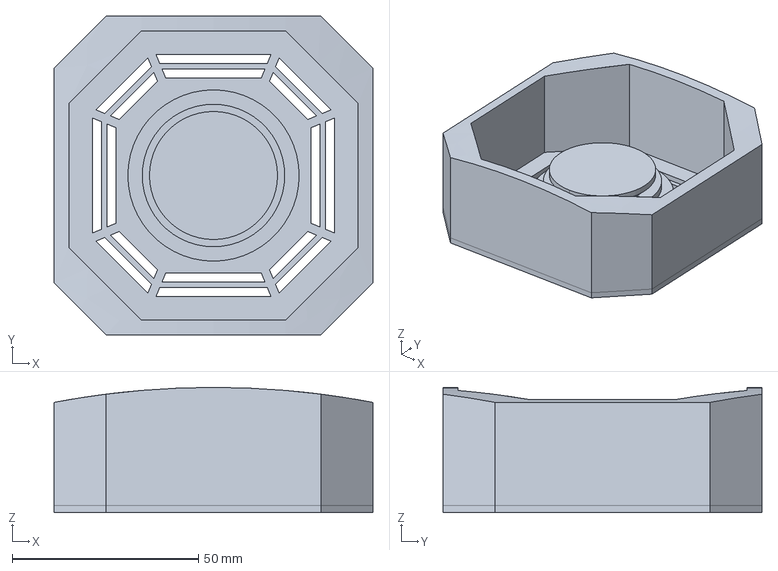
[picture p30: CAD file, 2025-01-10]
ref/blueprints/csr/cad/CSR OCTAGON PORT ASSY ANH - 20140325.igs
85.7 x 85.7 x 33.7 mm

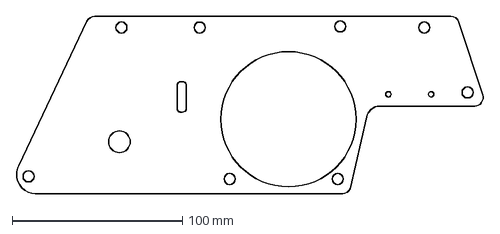
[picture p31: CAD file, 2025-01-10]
ref/guides/solaris/foot-frame-outer/Inner Main Panel.dxf
274.2 x 104.1 mm

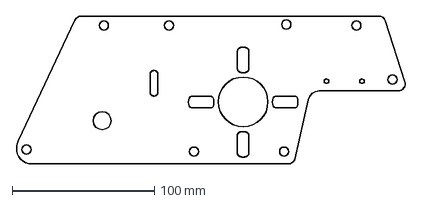
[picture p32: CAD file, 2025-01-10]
ref/guides/solaris/foot-frame-outer/Outer Main Panel.dxf
274.2 x 104.1 mm

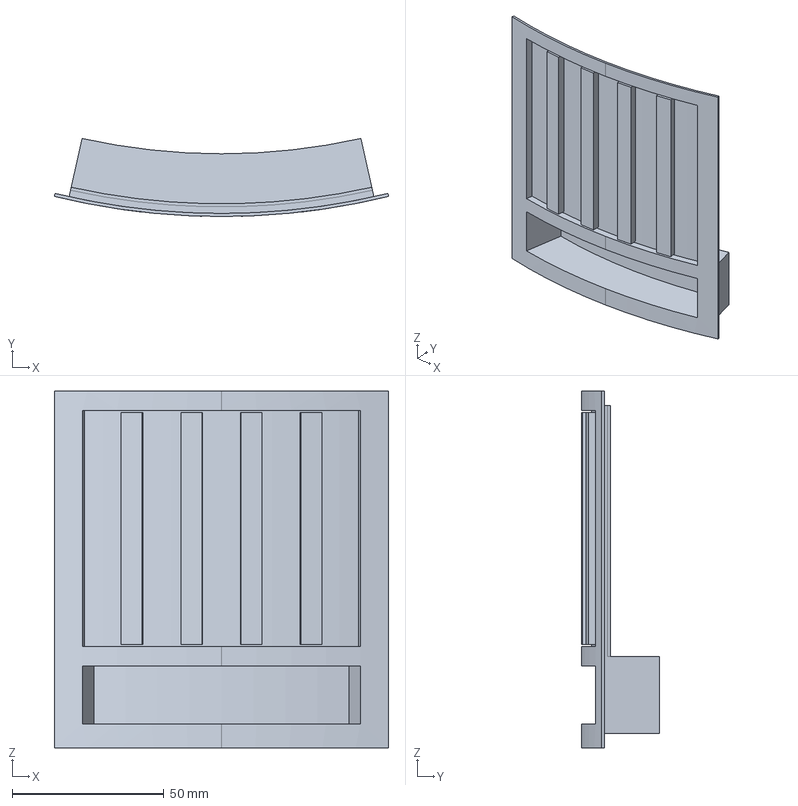
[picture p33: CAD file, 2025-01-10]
ref/blueprints/csr/cad/CSR POCKET VENT ASSY ANH - 20140325.igs
110.1 x 25.7 x 117.5 mm

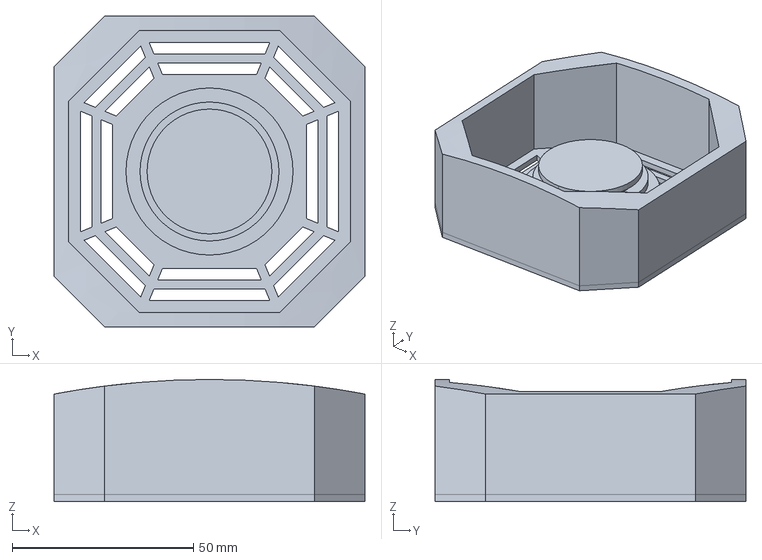
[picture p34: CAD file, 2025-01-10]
ref/blueprints/csr/cad/CSR OCTAGON PORT ASSY ESB - 20140325.igs
85.7 x 85.7 x 33.7 mm

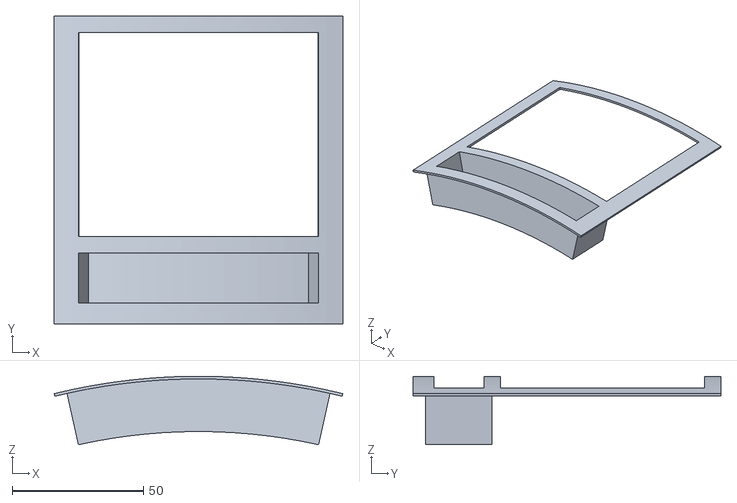
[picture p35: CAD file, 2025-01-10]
ref/guides/solaris/pocket-vent_front/stl/Main Body.stl
110.1 x 117.5 x 26.1

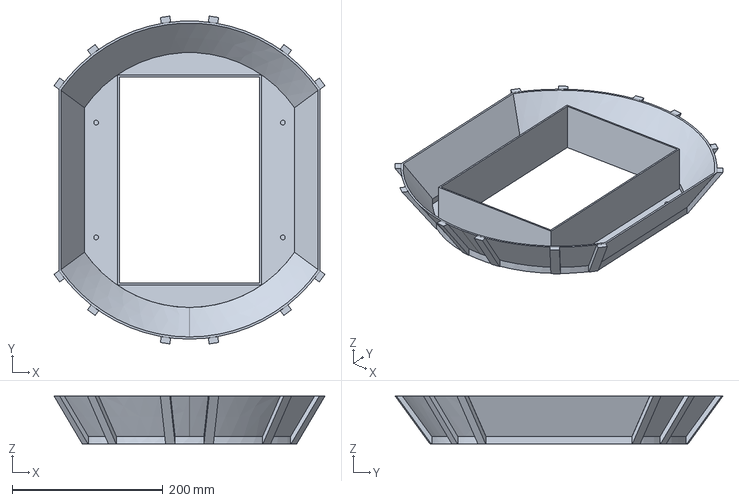
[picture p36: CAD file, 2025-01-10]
ref/blueprints/csr/cad/CSR Skirt Assy - 20140501.igs
359.7 x 435.1 x 63.5 mm

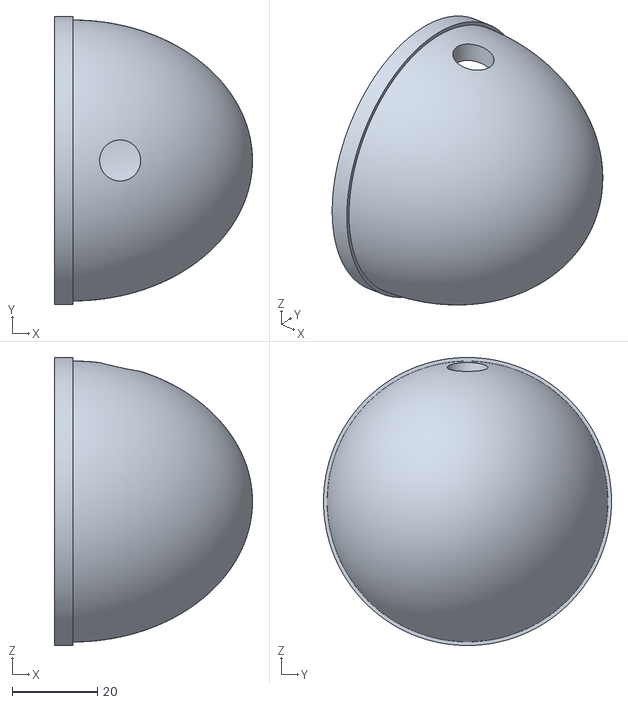
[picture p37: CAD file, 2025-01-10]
ref/guides/robby-head_dome/Head/Left Eye/Main Cone.stl
46.6 x 67.7 x 67.7

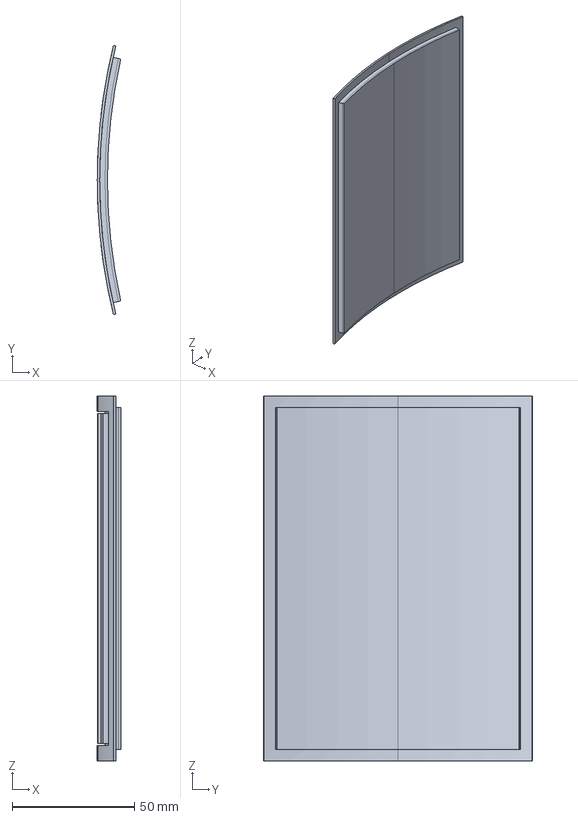
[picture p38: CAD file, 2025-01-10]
ref/blueprints/csr/cad/CSR SIDE VENT ASSY ANH - 20140325.igs
9.63 x 110.1 x 149.2 mm

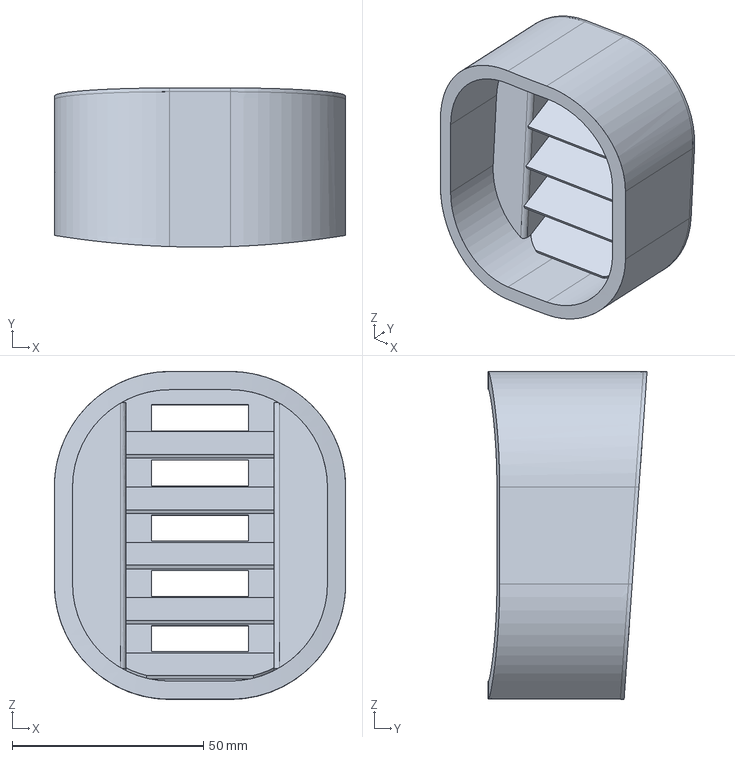
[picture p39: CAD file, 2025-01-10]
ref/blueprints/csr/cad/CSR Center Vent Assy Bottom - 20140502.igs
76.2 x 41.6 x 85.8 mm

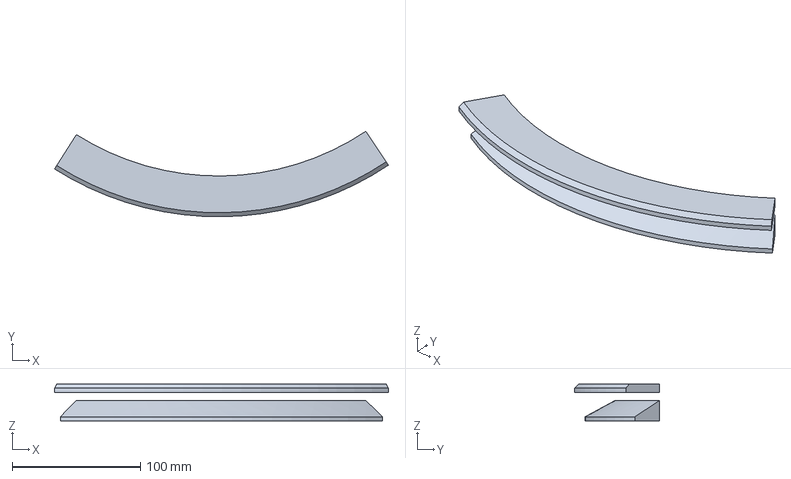
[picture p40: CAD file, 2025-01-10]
ref/blueprints/csr/cad/CSR Large Data Port Assy - 20140329.igs
260.2 x 66.6 x 28.6 mm

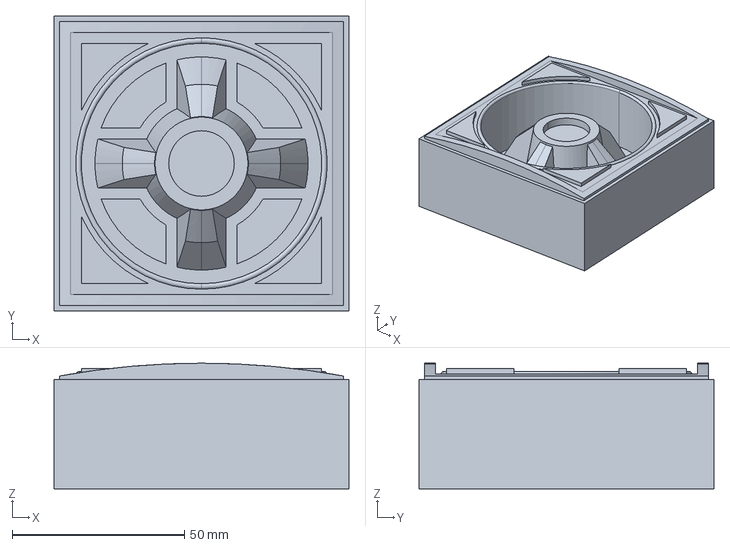
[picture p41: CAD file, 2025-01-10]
ref/blueprints/csr/cad/CSR POWER COUPLER ASSY - 20140325.igs
85.7 x 85.7 x 36.5 mm

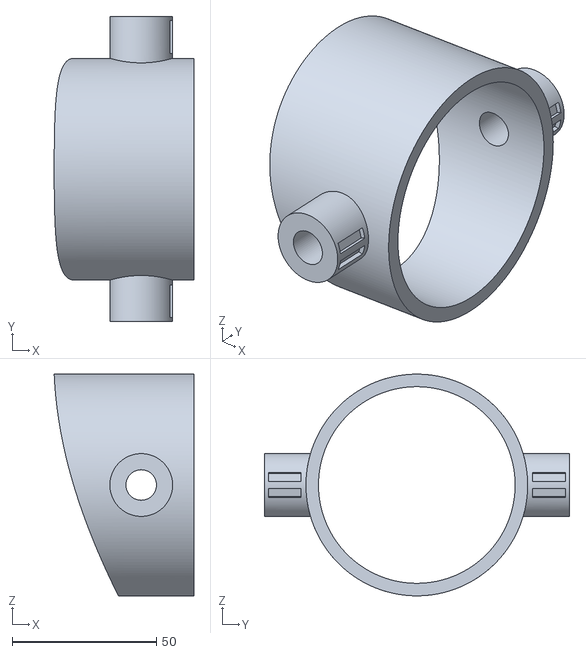
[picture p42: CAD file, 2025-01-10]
ref/guides/robby-head_dome/Head/Left Eye/Main Body.stl
48.4 x 105.7 x 76.9

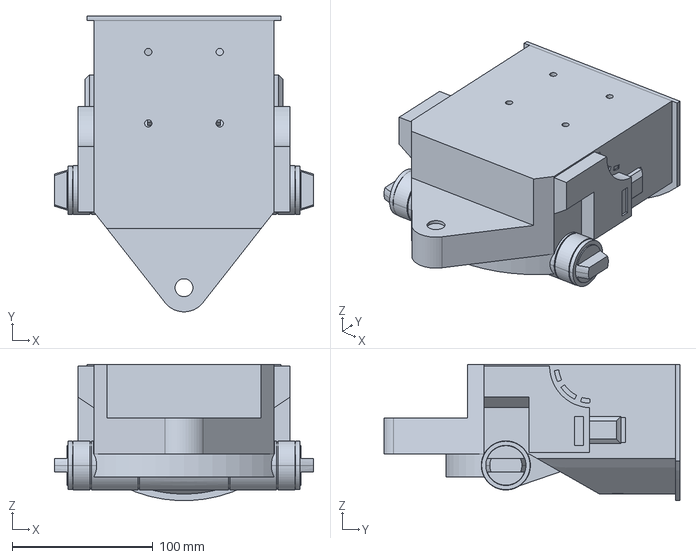
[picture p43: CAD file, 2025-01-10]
ref/blueprints/csr/cad/CSR Ankle Assembly Outer - 20140621.igs
184.1 x 210.2 x 96.7 mm

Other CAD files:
ref/blueprints/csr/cad/CSR Center Vent Assy Top - 20140502.igs
ref/blueprints/csr/logo/CSR Logo 2D.igs
ref/guides/robby-head_dome/Dome.stl
ref/blueprints/csr/cad/ANH-skins_1.dxf
ref/blueprints/csr/cad/CSR ANKLE BRACELET - 20140610.igs
ref/blueprints/csr/cad/CSR ANKLE CYLINDER - 20140610.igs
ref/blueprints/csr/cad/CSR ANKLE CYLINDER HOLDER - 20140610.igs
ref/blueprints/csr/cad/CSR ANKLE CYLINDER WEDGE - 20140610.igs
ref/blueprints/csr/cad/CSR ANKLE DETAIL - 20140612.igs
ref/blueprints/csr/cad/CSR ANKLE OUTER - 20140610.igs
ref/blueprints/csr/cad/CSR Coin Return - Front 20140329.igs
ref/blueprints/csr/cad/CSR Coin Return - Rear Left 20140329.igs
ref/blueprints/csr/cad/CSR Coin Return - Rear Right 20140329.igs
ref/blueprints/csr/cad/CSR Coin Slots - 20120811.igs
ref/blueprints/csr/cad/CSR R5 ANTENNA - 20140529.igs
ref/blueprints/csr/cad/CSR Radar Eye - 20140513.igs
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

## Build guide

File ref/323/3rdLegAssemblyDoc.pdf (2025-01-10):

R2D2 3

rd

# leg mechanism assembly V1.0

### Mike.Lambert1@NTLWorld.com

Or

### Mike_Grafix@Hotmail.com

Please read these instructions before commencing.

The first stage is to modify the frames existing Ring 2. This will need 3 holes drilled (6mm) and a cut out. The holes should be as accurate as possible but if this is not possible then drill them slightly larger to take up any inaccuracy. The cut out doesn’t have to be accurate. Just as neat as possible and adequate. Its purpose is to provide clearance. Drawings are supplied for Ring 2.

Assemble the centre section using the nylon sliding parts and the upper and lower mounting plates. Do not over tighten. This will miss form the nylon sliding parts and cause the mechanism to bind. Look at the diagram for the nuts, bolts and washers. After assembly place the 4 off bearing rods through the sliding and check for fit. These should be able to slide up and down with ease. If they are sticking slightly slacken off the bolts through the sliding parts. Spring washers are included in the kit to aid in anti vibration. The upper plate has a large hole and 4 off M5 holes. This is for possible future use and no parts are missing from the kit. The lower plate has 8 off 6mm holes for mounting the 3

rd
foot
adaptor plate that is designed and supplied by Guy Averett.

Next, place the nylon bearing rod holders onto the bearing rods ensuring that the threaded end is not in the nylon bearing holder and place the assembly into the frame of the robot. The upper bearing rods align with the frames existing holes in ring 2. Align the nylon bearing holders in the lower set of holes in ring 5 of the frame and loosely place the counter sunk M6 screws. Slide the centre assembly up so that it sits on ring 2, place washers and bolts through the existing ring 2 holes into the bearing rods and lightly tighten. Check for free un-bound movement in the mechanism. If there is sticking then slacken the bolts and move the offending bearing rod slightly to fix this. It may be necessary to slightly drill out the holes in ring 2 to allow for more movement. Take your time with this step. When you are satisfied with free unbound travel tighten the upper and lower bearing rods and mounting block screws.

DO NOT LUBRICATE. Nylon is a self lubricating material and needs no lubrication. If you do lubricate with oil or grease then over time particles of dirt, grit and other foreign objects will stick to the bearing rods or sliding parts causing them to wear out and or either bind or seize.

The satellite motor is now fitted to the motor mount using the supplied M5 countersunk screws. . It may be necessary to file down the sides on the heads of the screws on the satellite motors rear casing. I have found some motors that use heads that protrude from the side of the motor casing. This causes the motor assembly to be difficult to fit into the mount. The motor mount is then fitted to Ring 2 as shown on the drawing using the supplied washers and bolts.

Fit the motor arm to the satellite output using the shorter M6 countersunk screws. Fit the link arm making sure that the 8mm hole is to the satellite motor arm. Screw an M8 dome headed bolt through this hole into the motor arm and on the threaded part that protrudes from the motor arm fit the ½ M8 nut. Slightly tighten the M8 bolt to remove slop but not cause binding and then lock using the ½ M8 nut. Fit the other end of the link arm to the lower plate using a washer and bolt. This bolts shank will tighten on the lower plates threaded hole and enable a nice tight fit.

That’s the 3

rd
leg mechanism assembled.

Our development unit was driven at 24V with very satisfactory results. The brake is retained so that the leg can be locked down or up. However, with the gear ratio of the satellite motor and gearbox this may not be needed. Its just belts and braces.

The future :-

I developed this unit for Jon Reason. I also made him a JAG frame. I will be designing electronics and software to drive all 3 legs in 2-3-2 mode. It will have an input from the RC, drive both outer legs and the centre leg. The modifications needed will be micro switches fitted to the end stop positions of ALL the legs ( 6 switches in total ) and one micro switch fitted to some place in the mid travel position on the 3

rd
leg so that it moves and at a pre determined position it triggers the two outer legs. This unit will be fed with 24V, have onboard RC interface and 3 * H bridge FETs for all three motors as well as full control of the motors brakes.

The software and electronics will be made available to the group so that self build people can do it themselves.

I have also designed outer legs that have internal 2-3-2 actuation. I will be making the prototypes within the next 4 months for Jon and I will publish the final designs. There is a lot of machining and welding in the design but I think that the final product is well worth the effort.

If you have any comments then please contact me on either of the above email addresses.

Thankyou.

Mike Lambert.

The picture below shows Ring 2 and Ring 5 for illustration purposes only.

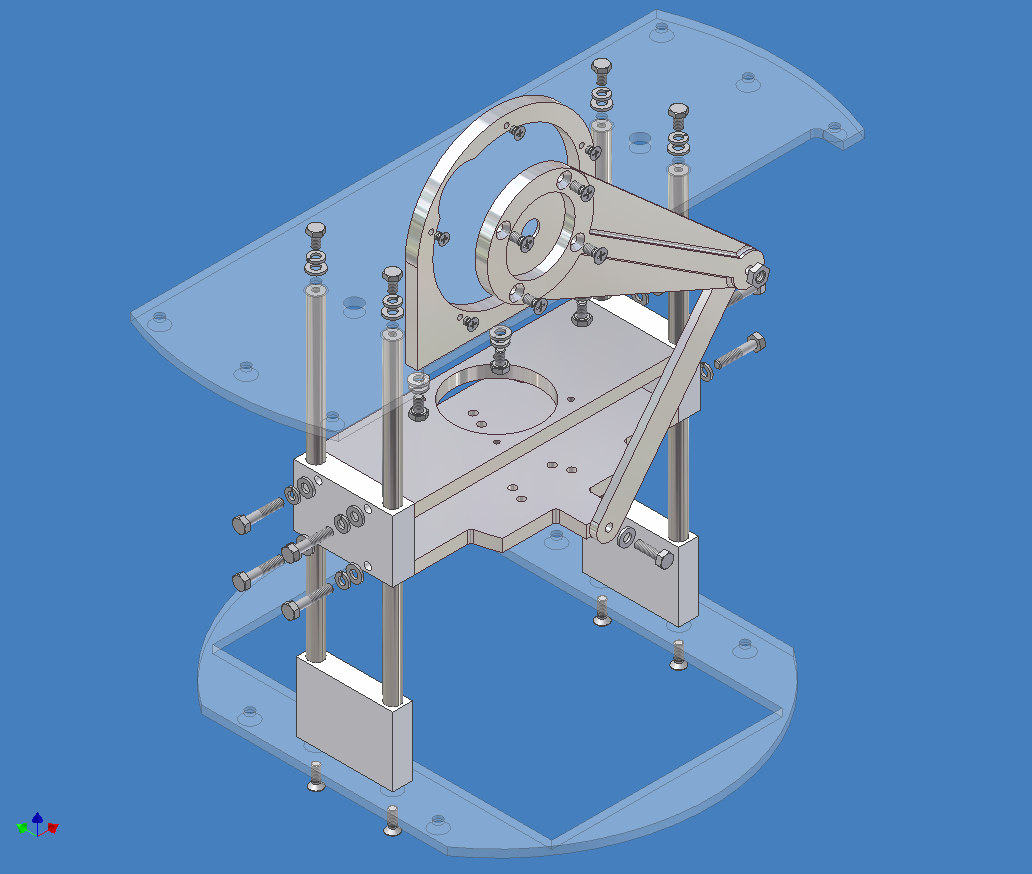
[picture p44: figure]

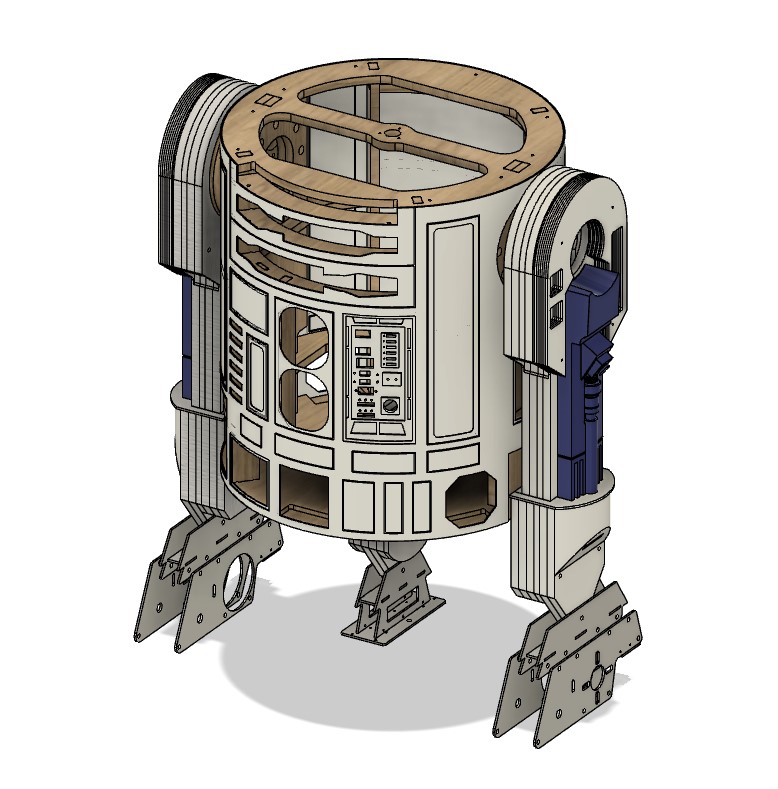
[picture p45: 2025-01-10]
ref/guides/solaris/Screenshot 2021-11-03 180305.jpg

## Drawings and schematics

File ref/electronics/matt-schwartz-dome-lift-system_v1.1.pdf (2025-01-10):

v1.1 - 10/2020

# www.printed-droid.com

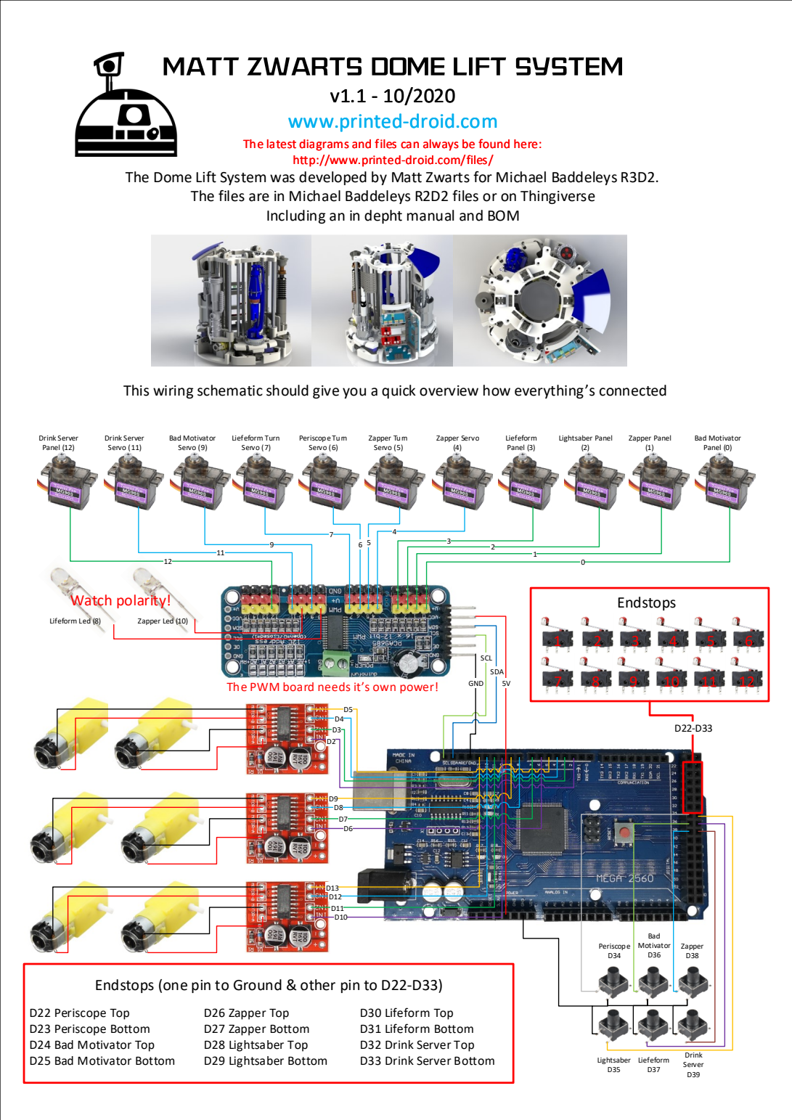
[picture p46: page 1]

www.printed-droid.com

The latest diagrams and files can always be found here:

http://www.printed-droid.com/files/

The Dome Lift System was developed by Matt Zwarts for Michael Baddeleys R3D2. (http://www.printed-droid.com/files/)

The files are in Michael Baddeleys R2D2 files or on Thingiverse

Including an in depht manual and BOM

This wiring schematic should give you a quick overview how everything’s connected

Endstops | 6 12

The PWM board needs it’s own power!

D13
D12

Endstops (one pin to Ground & other pin to D22-D33)

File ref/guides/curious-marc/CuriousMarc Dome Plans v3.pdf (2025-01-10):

P7

HP2

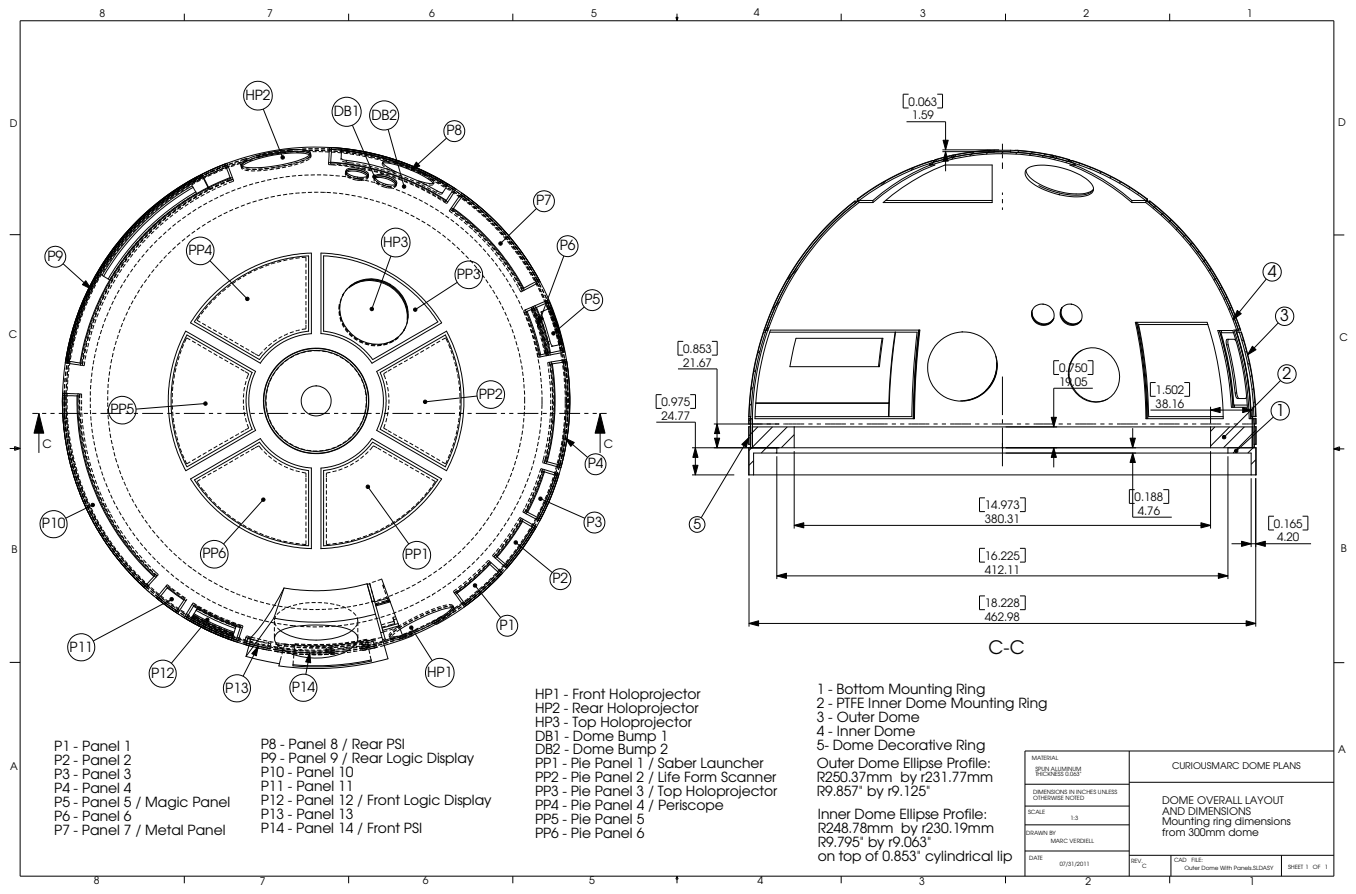
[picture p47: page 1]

HP1 - Front Holoprojector
HP2 - Rear Holoprojector
HP3 - Top Holoprojector
DB1 - Dome Bump 1
DB2 - Dome Bump 2
PP1 - Pie Panel 1 / Saber Launcher
PP2 - Pie Panel 2 / Life Form Scanner
PP3 - Pie Panel 3 / Top Holoprojector
PP4 - Pie Panel 4 / Periscope
PP5 - Pie Panel 5
PP6 - Pie Panel 6

1 - Bottom Mounting Ring
2 - PTFE Inner Dome Mounting Ring
3 - Outer Dome
4 - Inner Dome
5- Dome Decorative Ring
Outer Dome Ellipse Profile:
Inner Dome Ellipse Profile:
on top of 0.853" cylindrical lip

P8 - Panel 8 / Rear PSI
P9 - Panel 9 / Rear Logic Display
P10 - Panel 10
P11 - Panel 11
P12 - Panel 12 / Front Logic Display
P13 - Panel 13
P14 - Panel 14 / Front PSI

MATERIAL SPUN ALUMINUM THICKNESS 0.063" | CURIOUSMARC DOME PLANS

DIMENSIONS IN INCHES UNLESS OTHERWISE NOTED | DOME OVERALL LAYOUT AND DIMENSIONS Mounting ring dimensions from 300mm dome

145°

146.50°

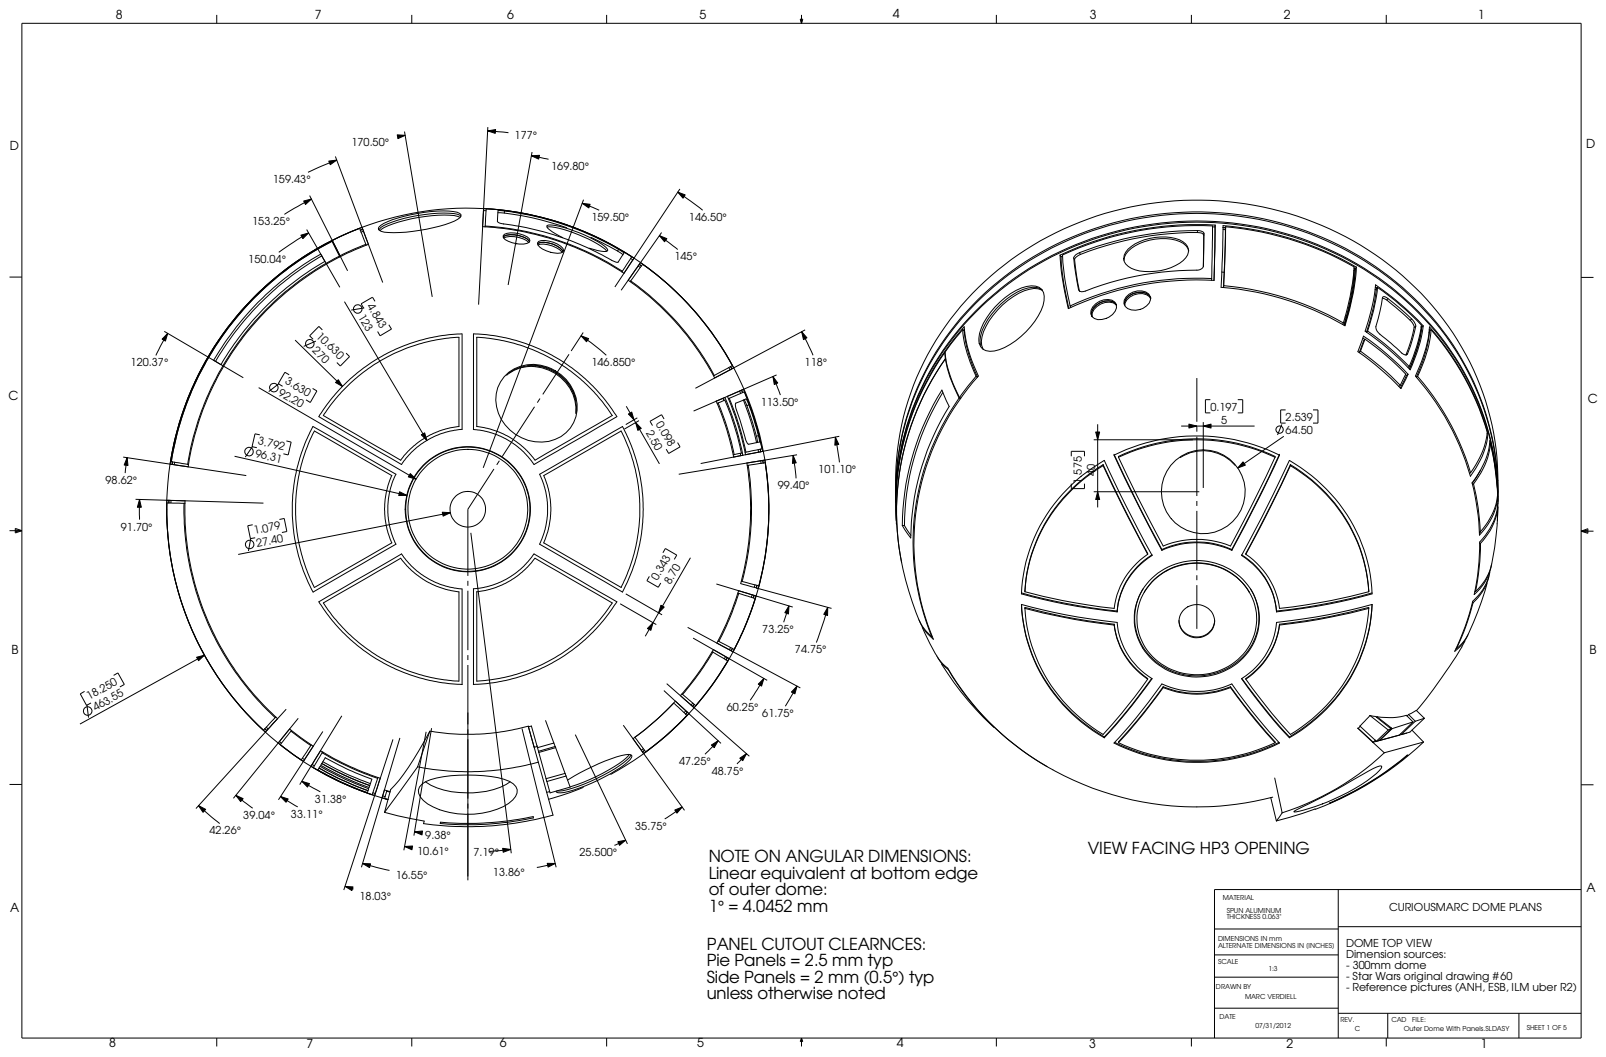
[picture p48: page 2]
DATE; REV.; CAD FILE:; SHEET 1 OF 5; SCALE

VIEW FACING HP3 OPENING NOTE ON ANGULAR DIMENSIONS:
Linear equivalent at bottom edge
of outer dome:

MATERIAL SPUN ALUMINUM THICKNESS 0.063" | CURIOUSMARC DOME PLANS

PANEL CUTOUT CLEARNCES:
Pie Panels = 2.5 mm typ
Side Panels = 2 mm (0.5°) typ
unless otherwise noted

DIMENSIONS IN mm ALTERNATE DIMENSIONS IN [INCHES] | DOME TOP VIEW Dimension sources: - 300mm dome - Star Wars original drawing # 60 - Reference pictures (ANH, ESB, ILM uber R2)

2.50 .51

D

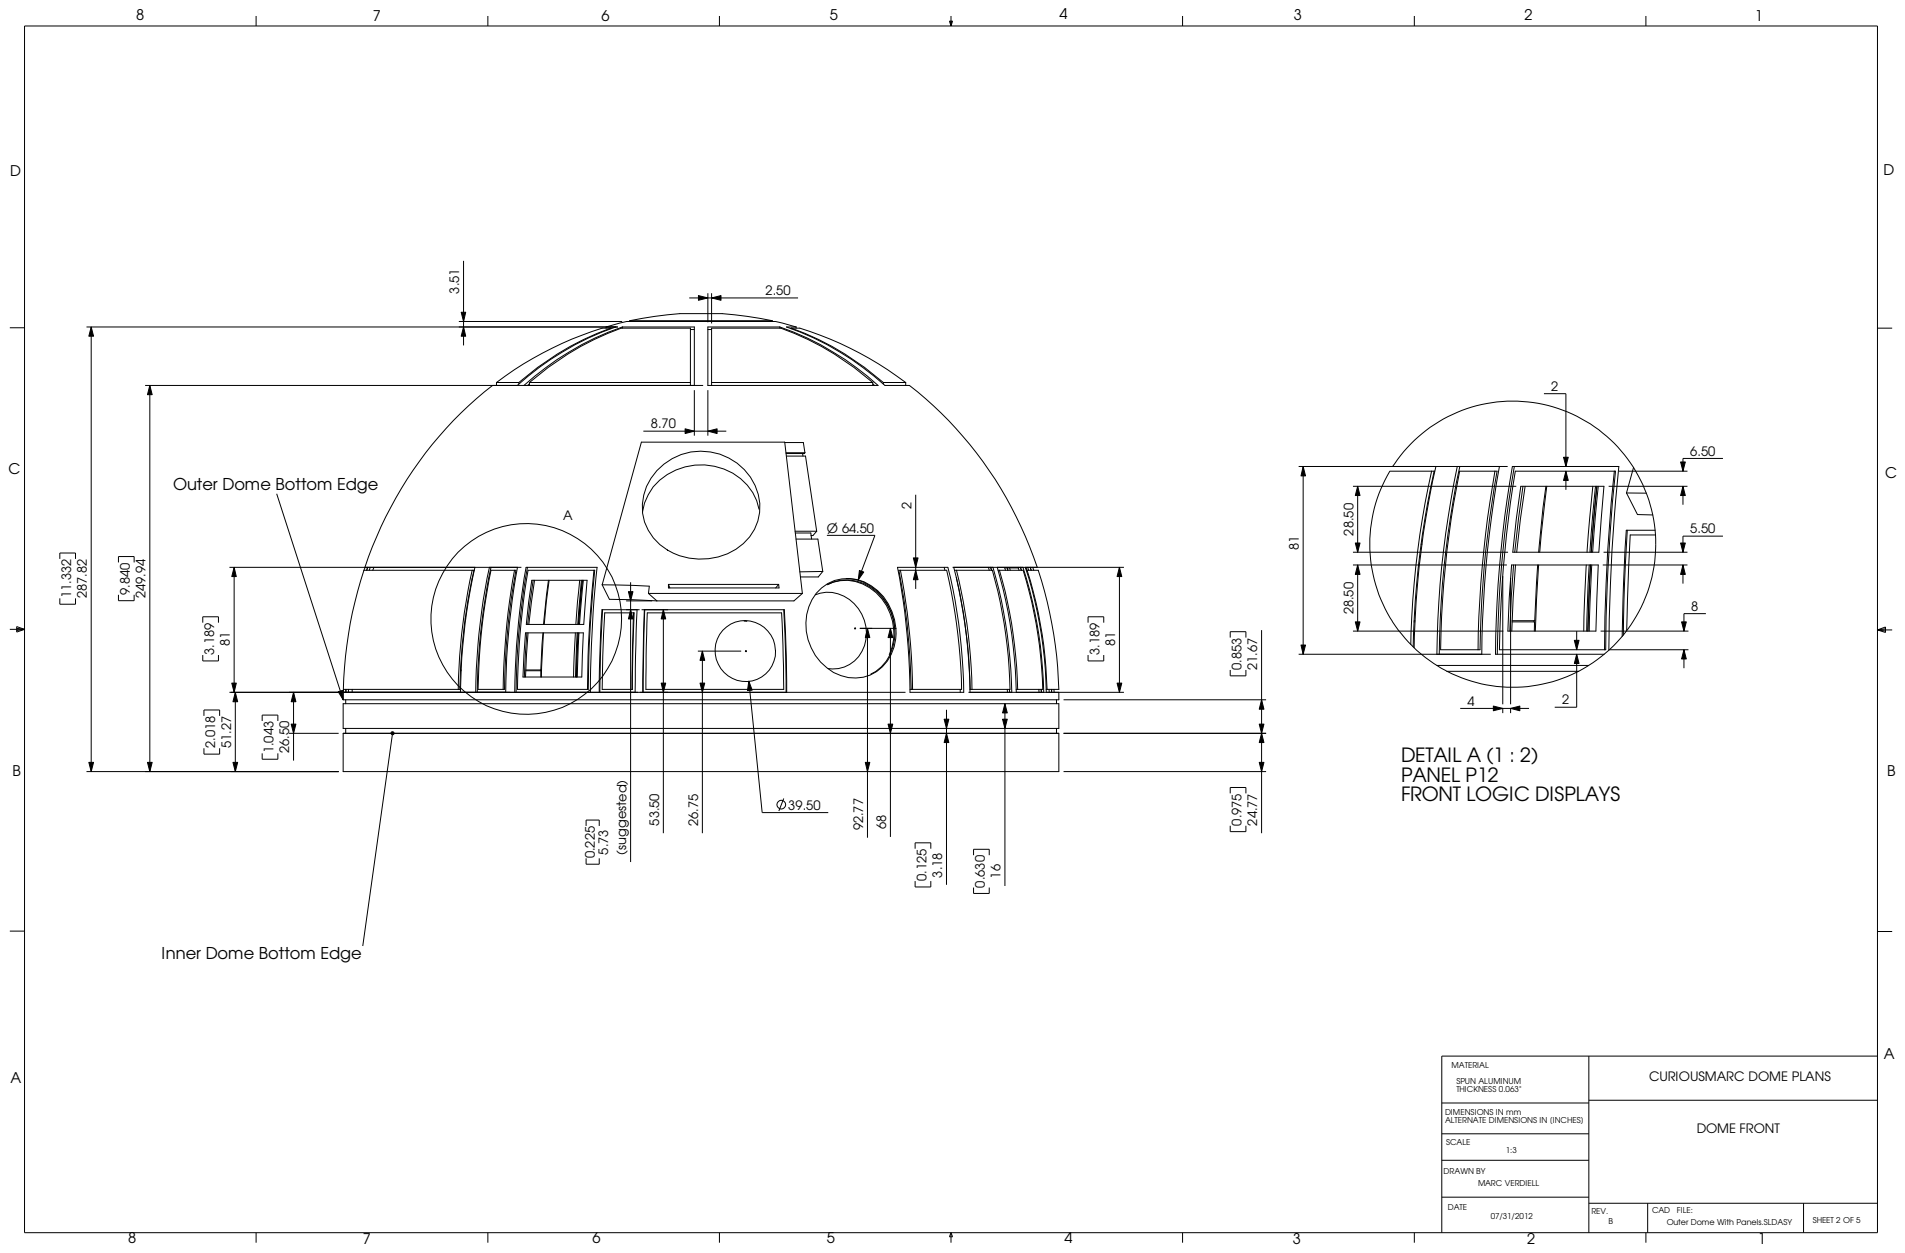
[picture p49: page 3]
(sug; este; REV.; CAD FILE:; SCALE; Outer Dome With Panels.SLDASY

Outer Dome Bottom Edge

DETAIL A (1 : 2)
PANEL P12
FRONT LOGIC DISPLAYS

Inner Dome Bottom Edge

MATERIAL SPUN ALUMINUM THICKNESS 0.063" | CURIOUSMARC DOME PLANS

DIMENSIONS IN mm ALTERNATE DIMENSIONS IN [INCHES] | DOME FRONT

3.331
84.60

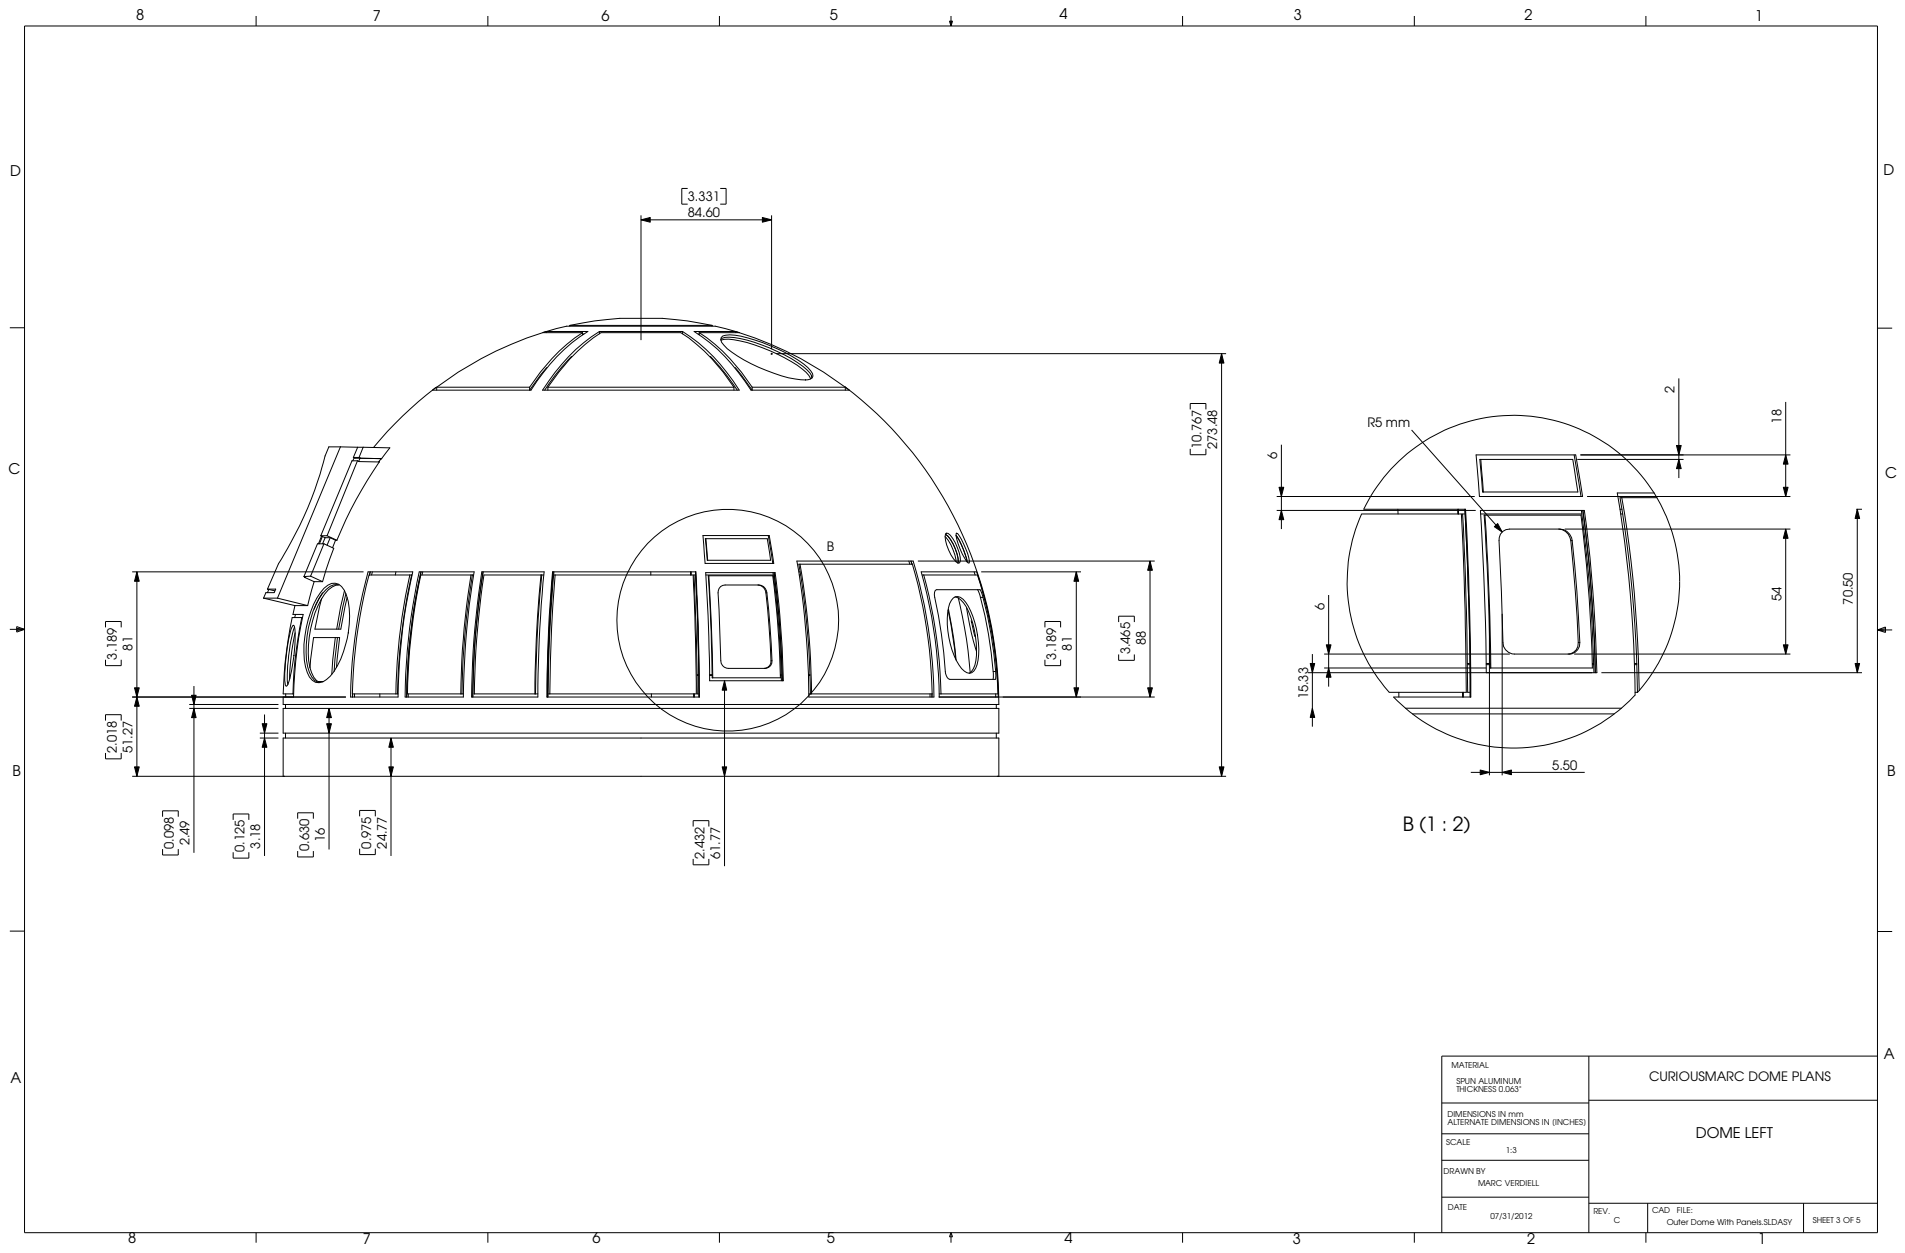
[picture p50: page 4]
SCALE

MATERIAL SPUN ALUMINUM THICKNESS 0.063" | CURIOUSMARC DOME PLANS

DIMENSIONS IN mm ALTERNATE DIMENSIONS IN [INCHES] | DOME LEFT

159.50° 166.80°

D

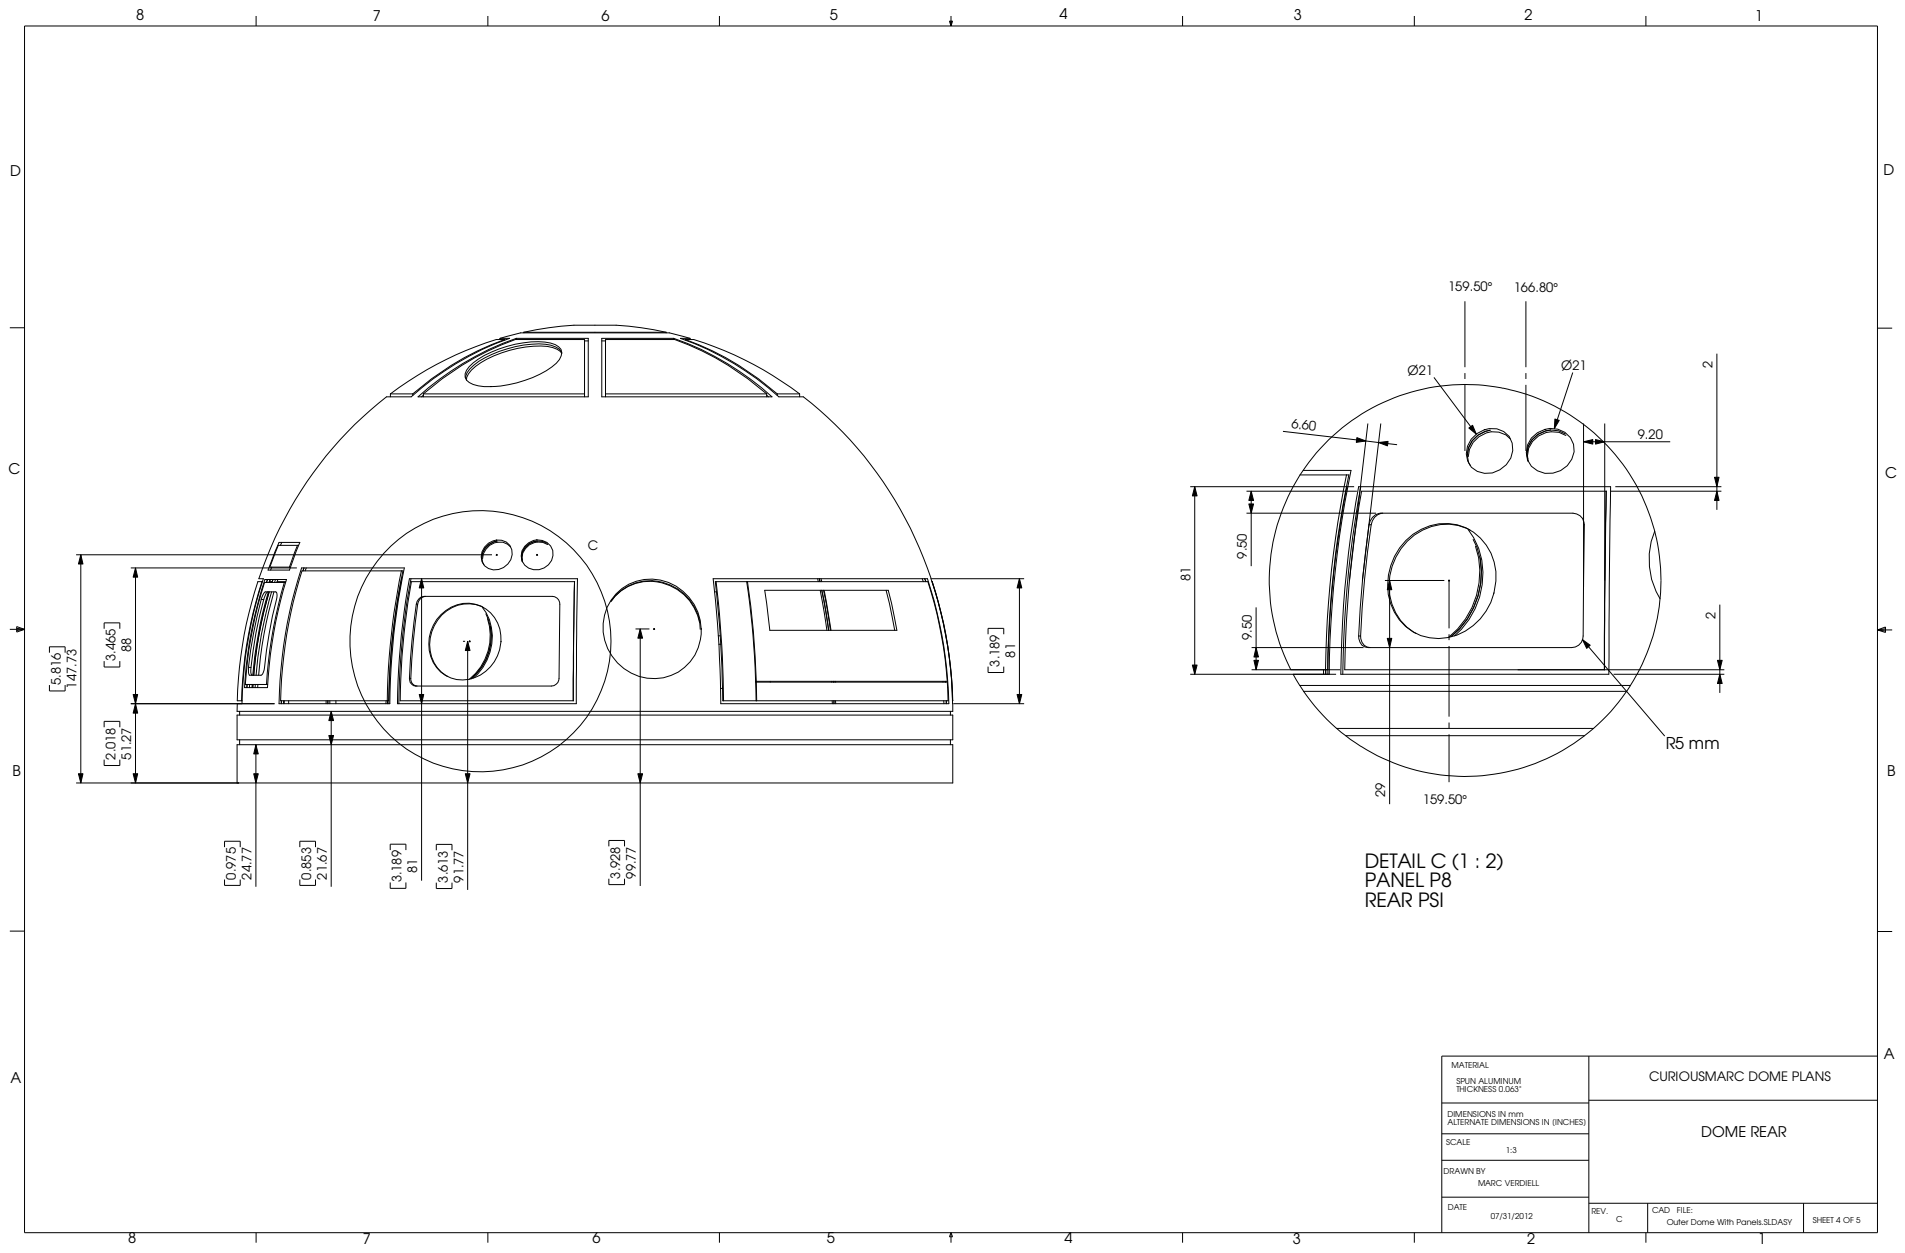
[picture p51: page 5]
DETAIL C (1 : 2) PANEL P8 REAR PSI; SCALE

MATERIAL SPUN ALUMINUM THICKNESS 0.063" | CURIOUSMARC DOME PLANS

DIMENSIONS IN mm ALTERNATE DIMENSIONS IN [INCHES] | DOME REAR

D
D

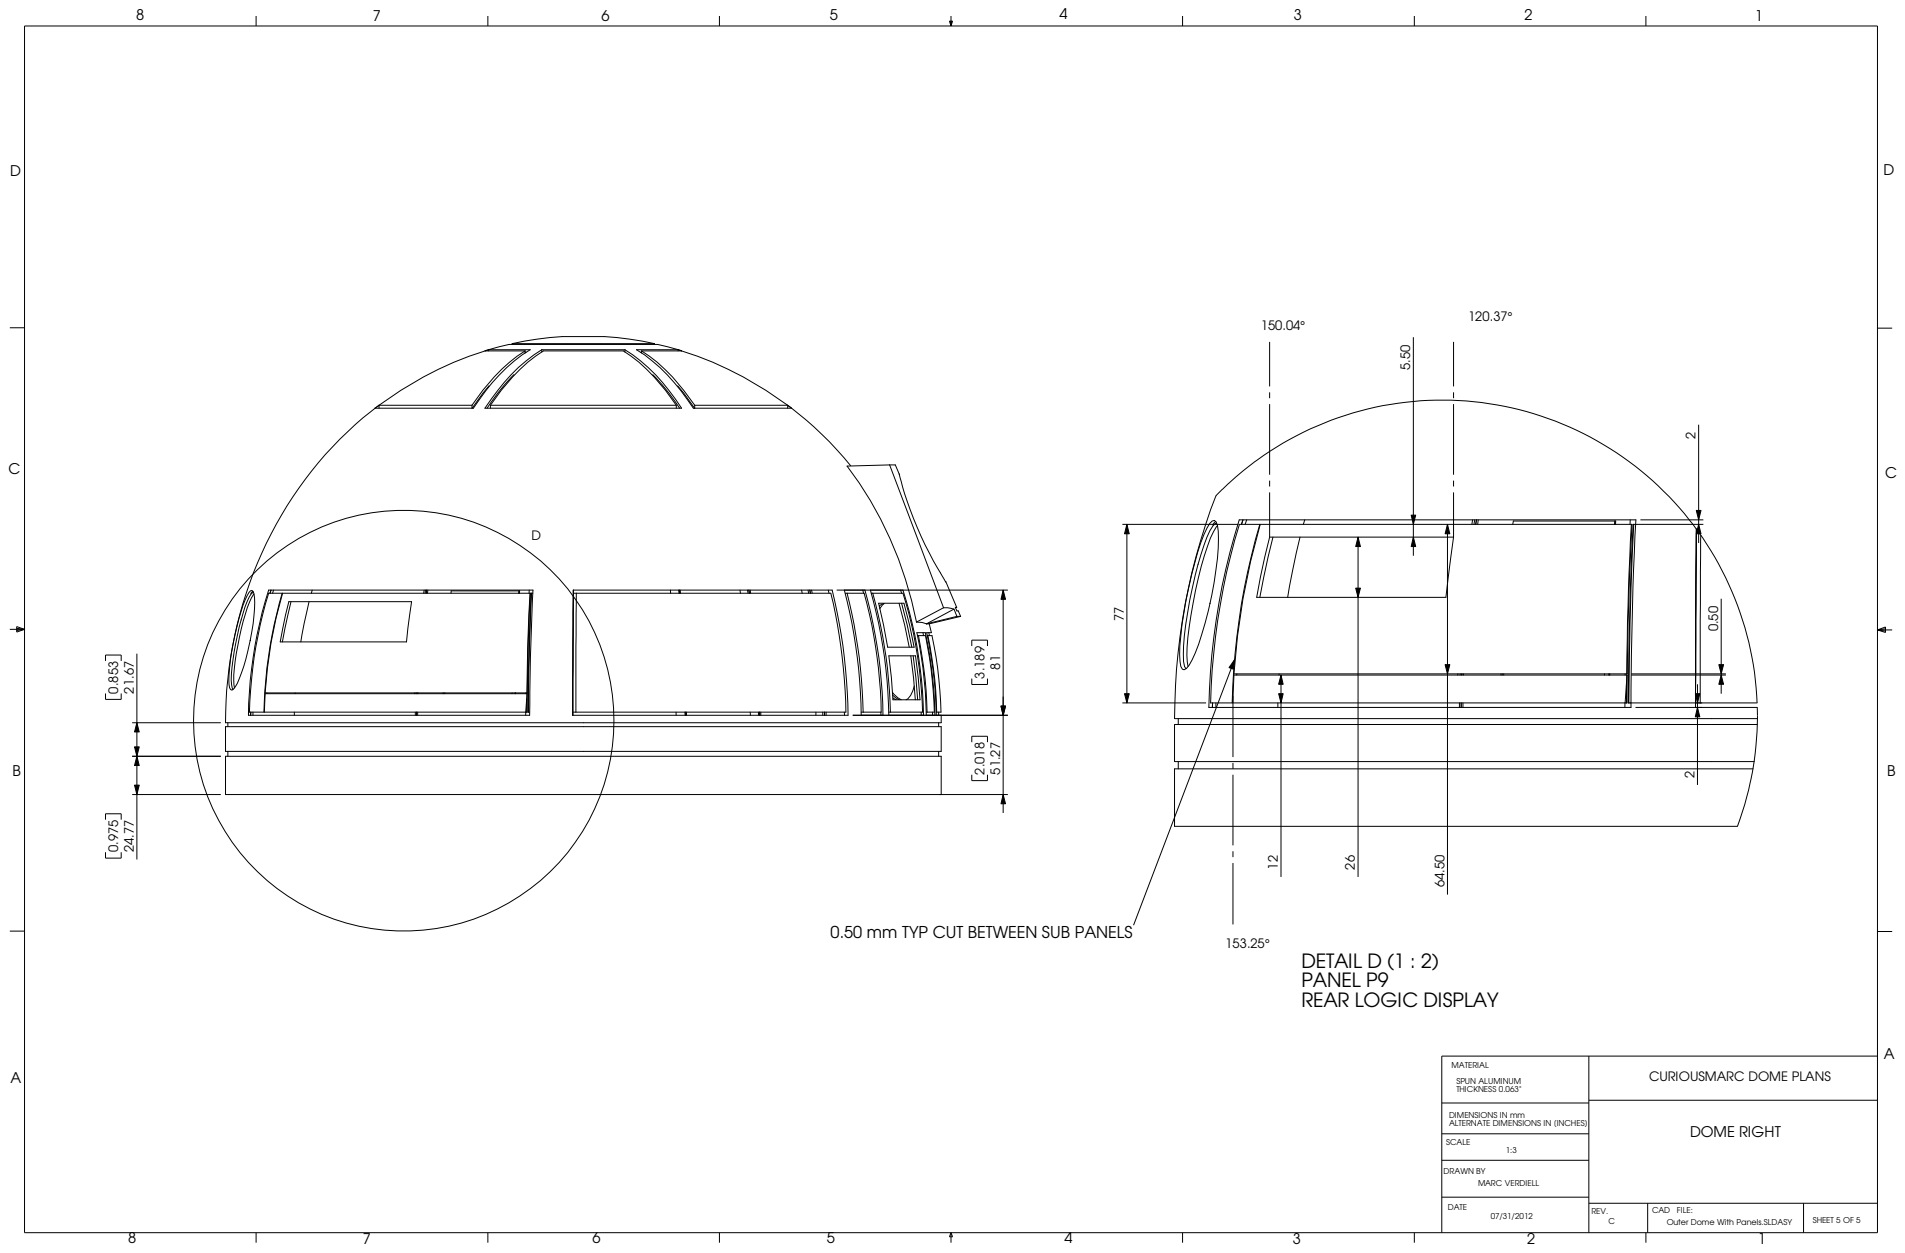
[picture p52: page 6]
SCALE

153.25° 0.50 mm TYP CUT BETWEEN SUB PANELS

DETAIL D (1 : 2)
PANEL P9
REAR LOGIC DISPLAY

MATERIAL SPUN ALUMINUM THICKNESS 0.063" | CURIOUSMARC DOME PLANS

DIMENSIONS IN mm ALTERNATE DIMENSIONS IN [INCHES] | DOME RIGHT

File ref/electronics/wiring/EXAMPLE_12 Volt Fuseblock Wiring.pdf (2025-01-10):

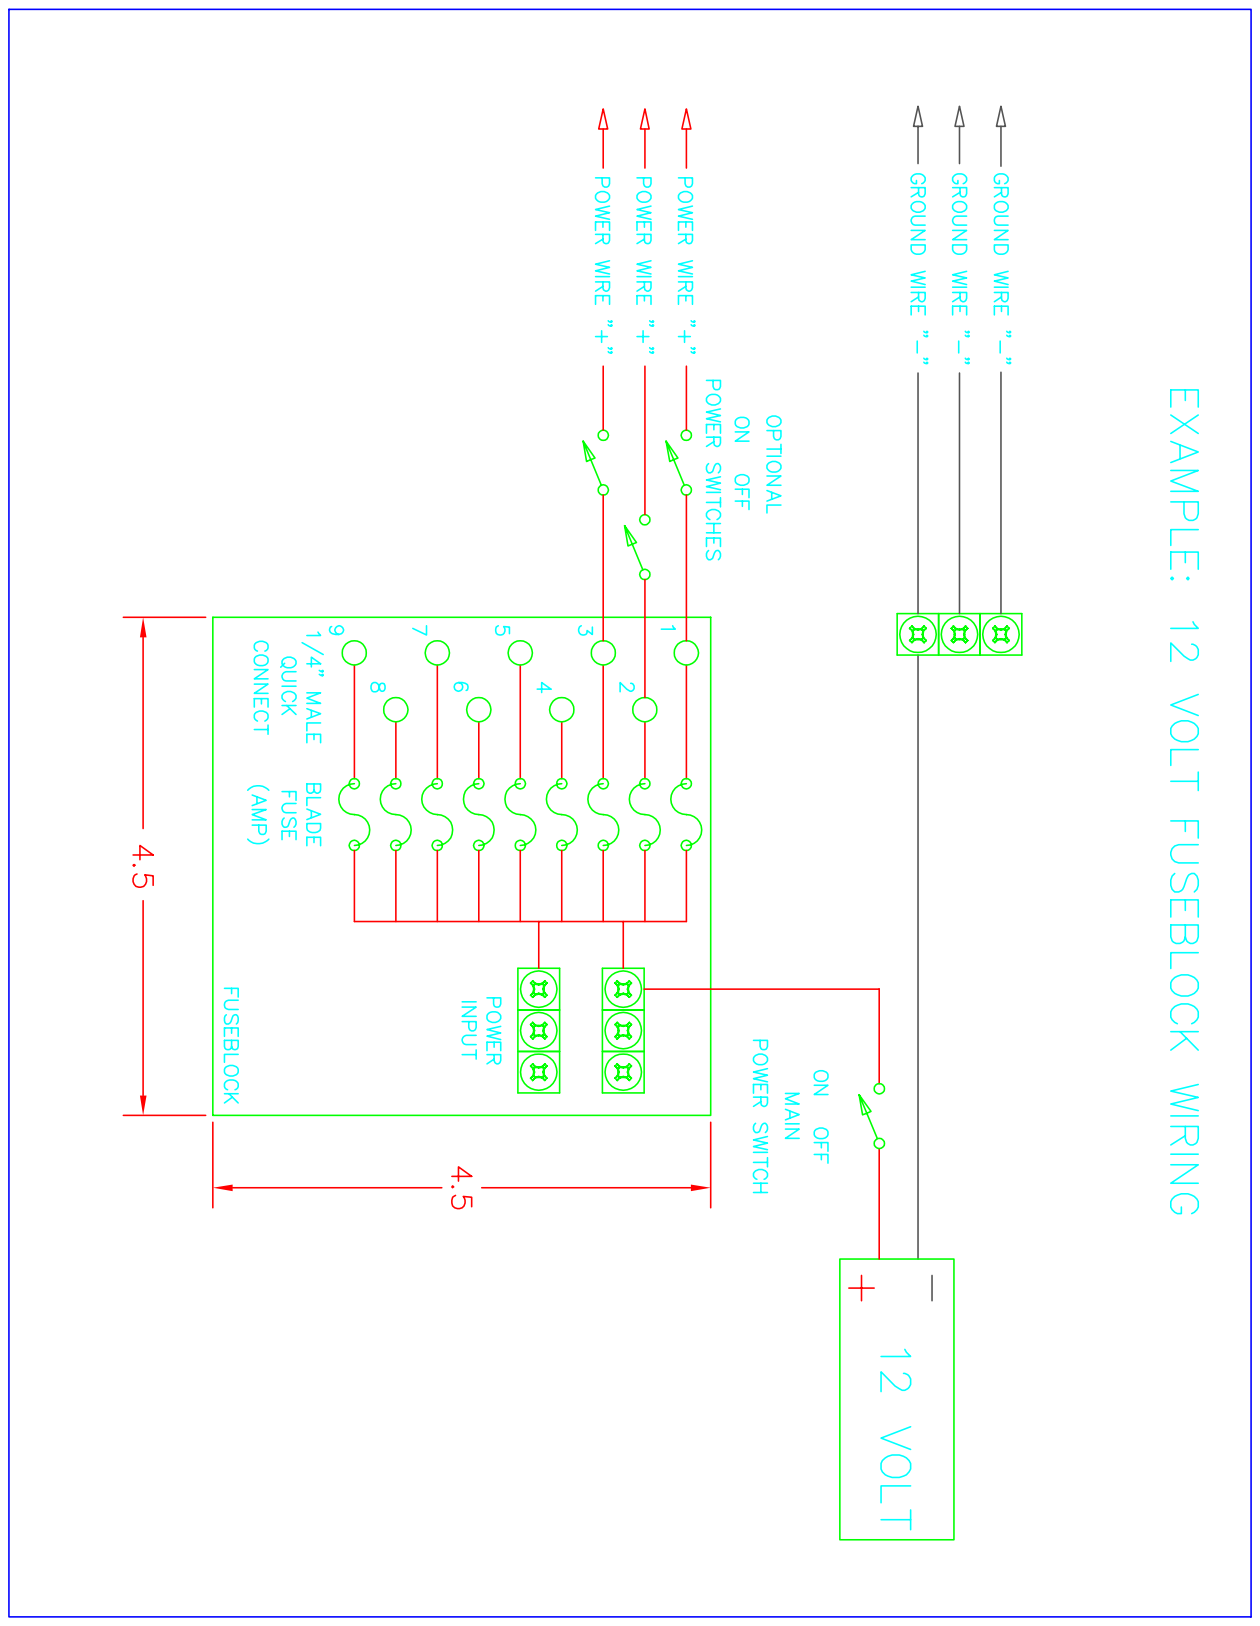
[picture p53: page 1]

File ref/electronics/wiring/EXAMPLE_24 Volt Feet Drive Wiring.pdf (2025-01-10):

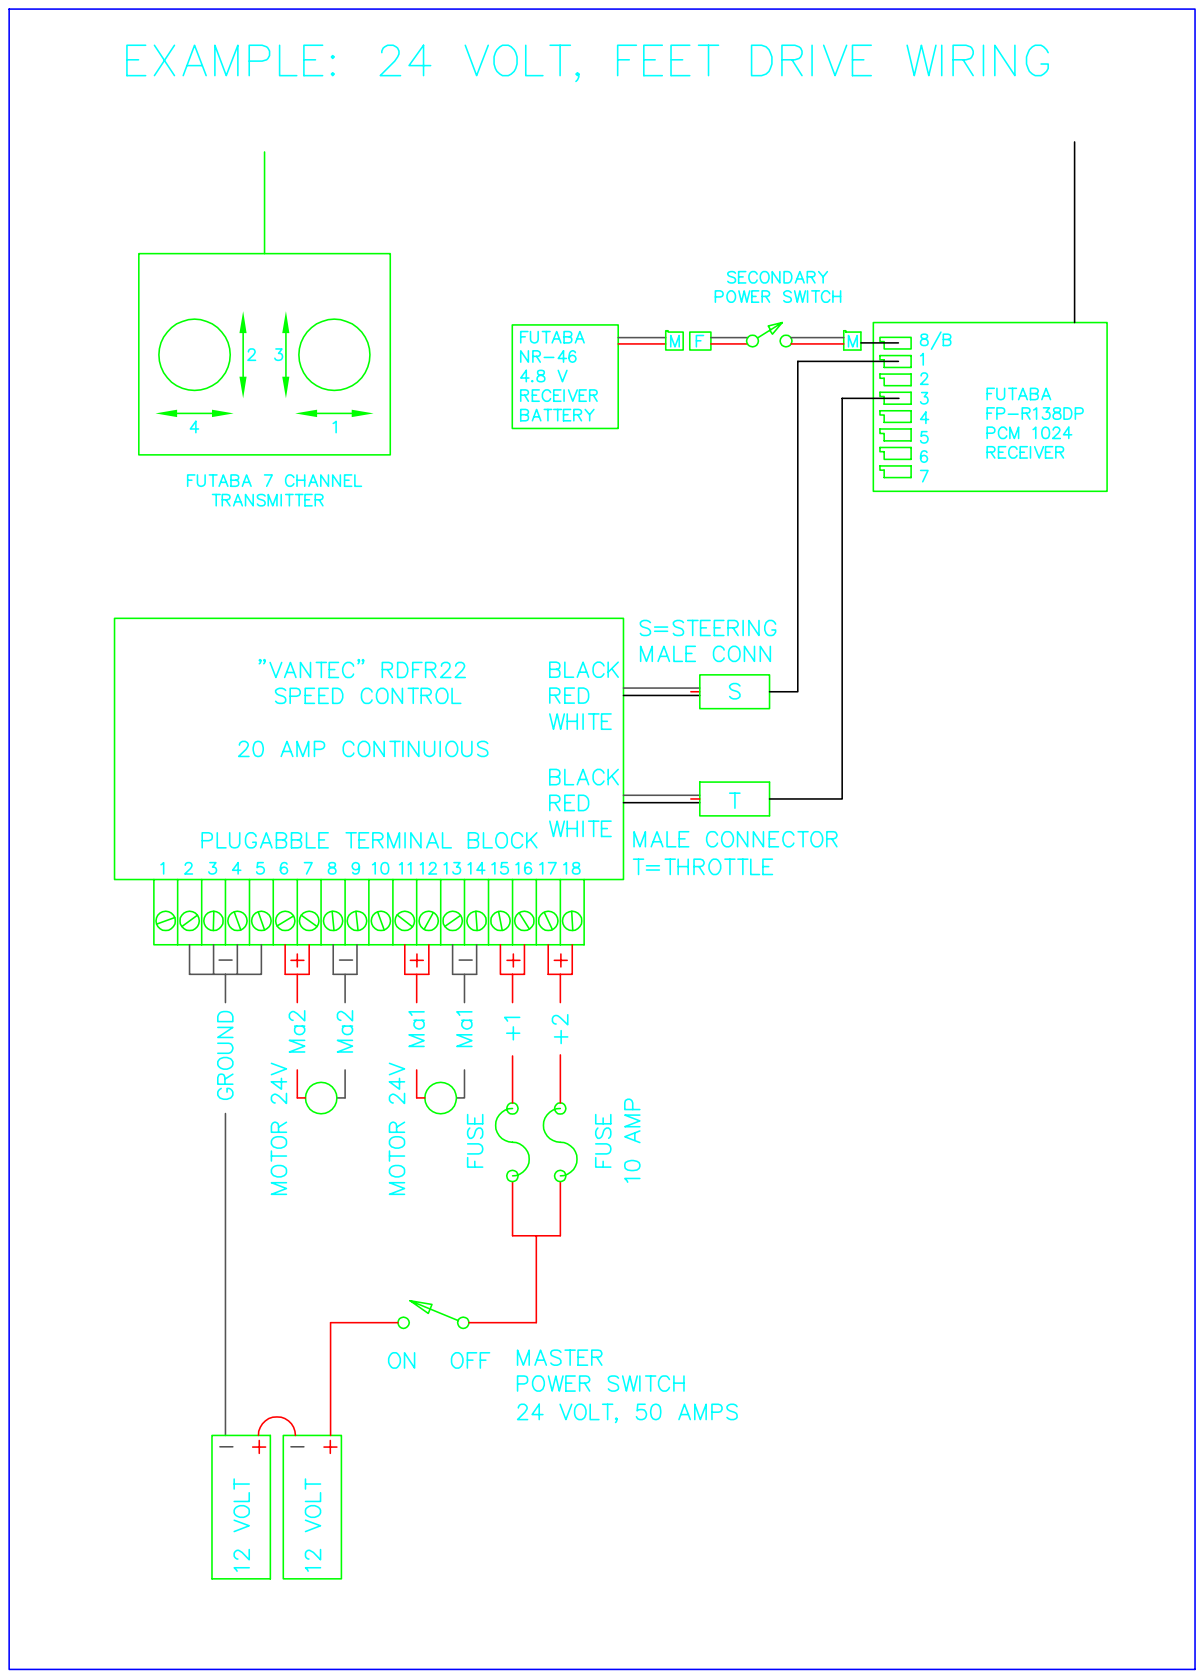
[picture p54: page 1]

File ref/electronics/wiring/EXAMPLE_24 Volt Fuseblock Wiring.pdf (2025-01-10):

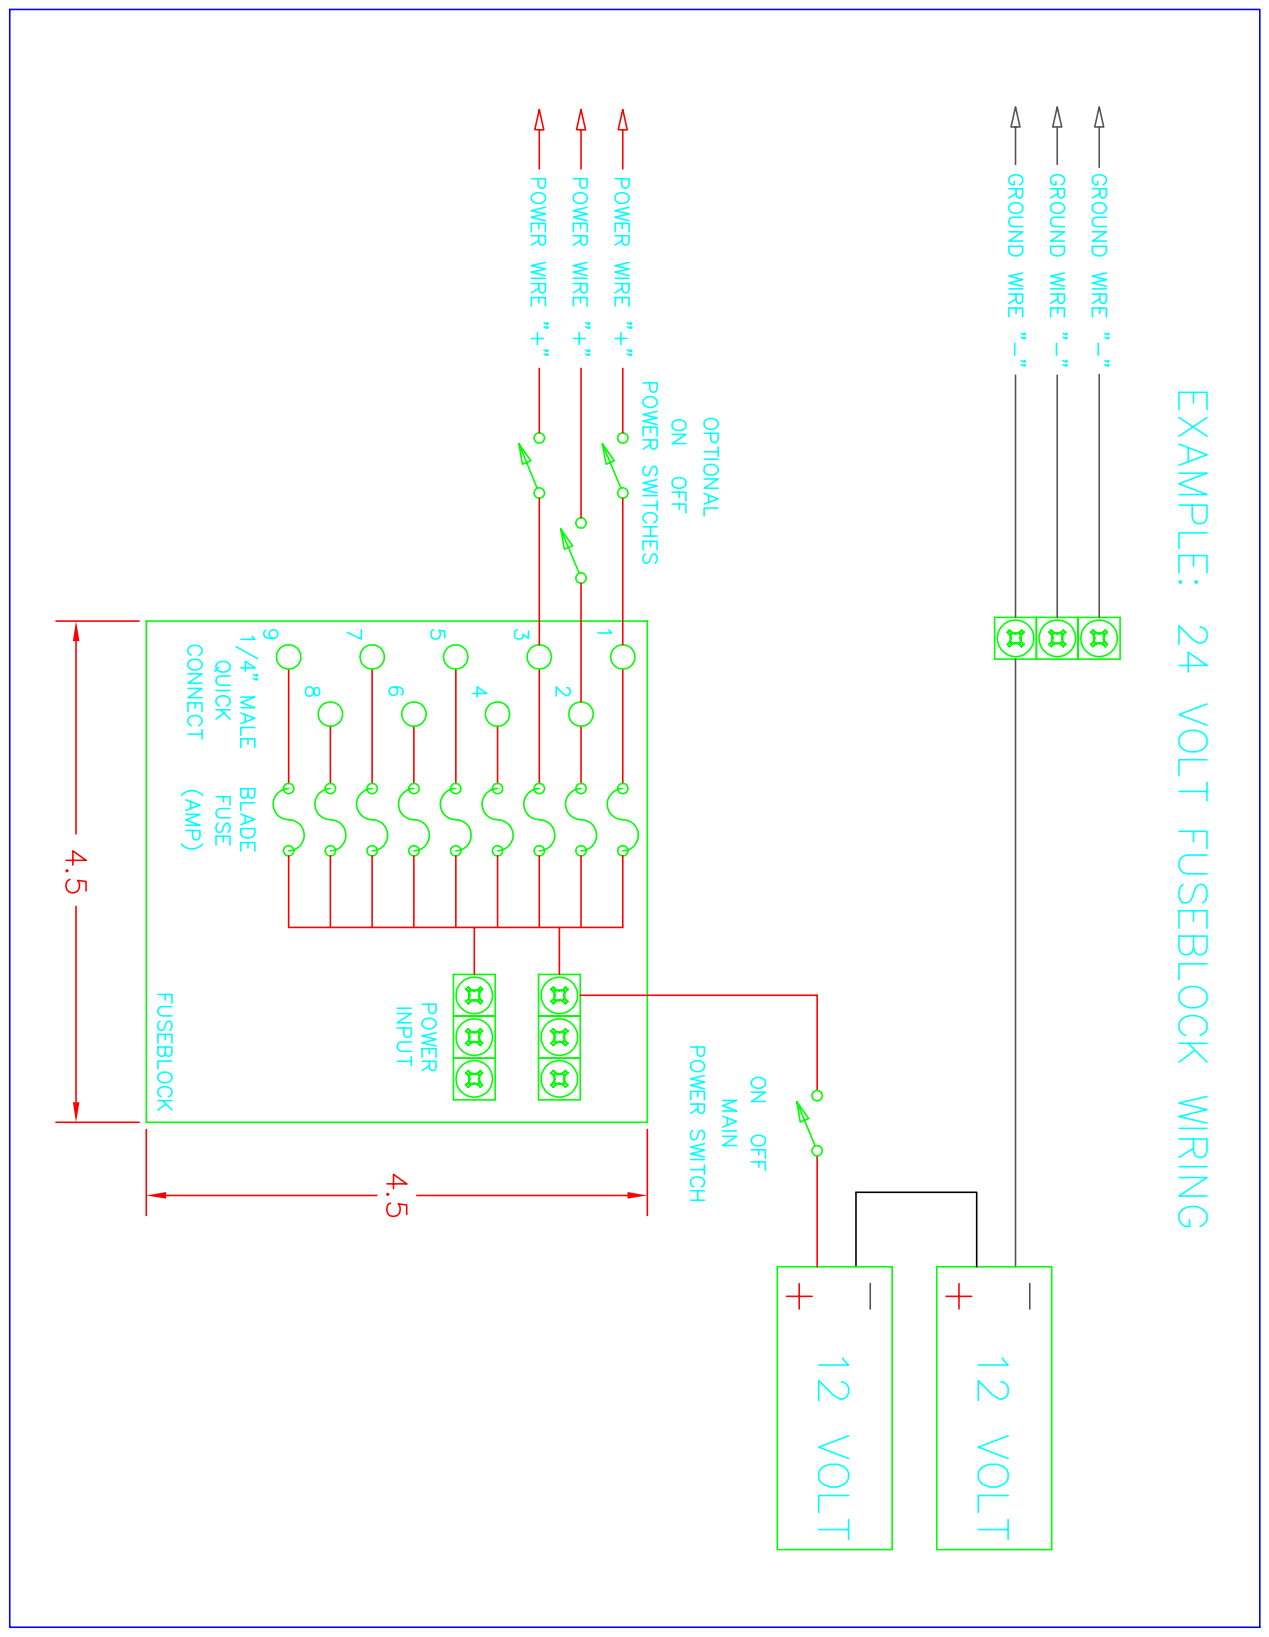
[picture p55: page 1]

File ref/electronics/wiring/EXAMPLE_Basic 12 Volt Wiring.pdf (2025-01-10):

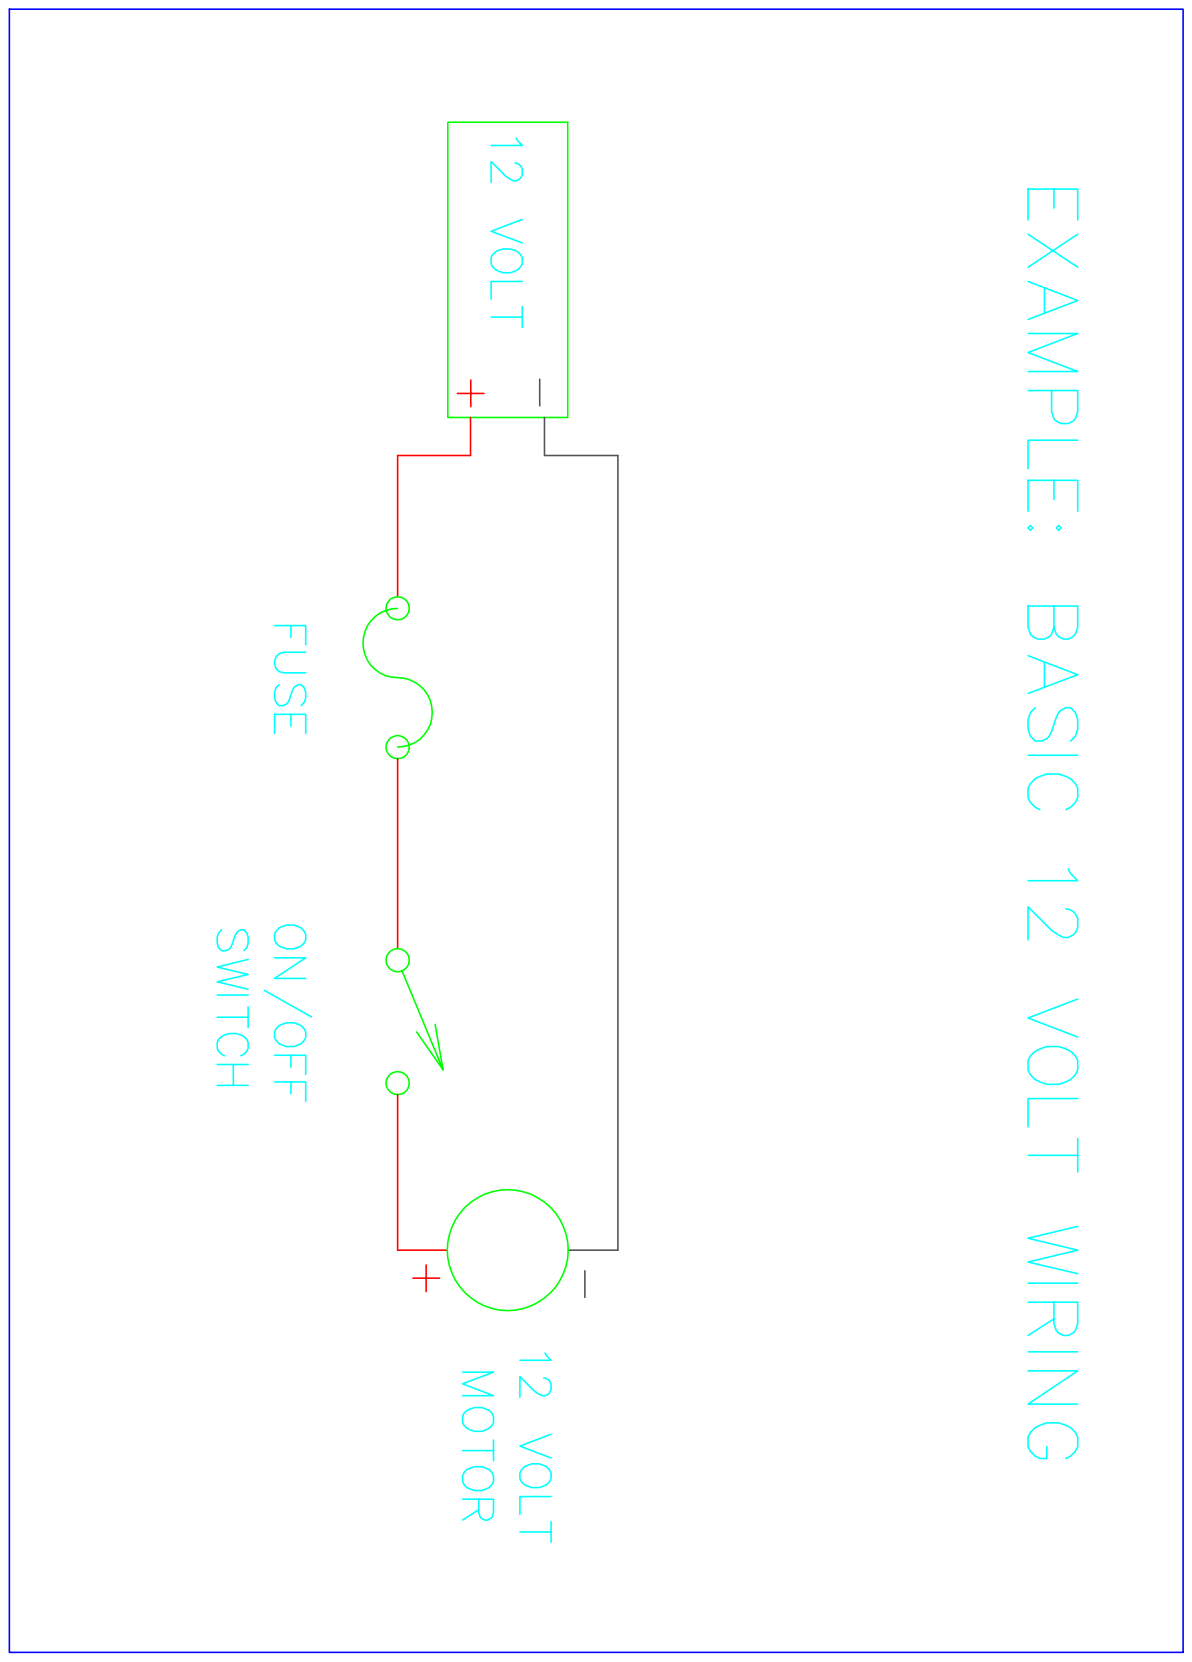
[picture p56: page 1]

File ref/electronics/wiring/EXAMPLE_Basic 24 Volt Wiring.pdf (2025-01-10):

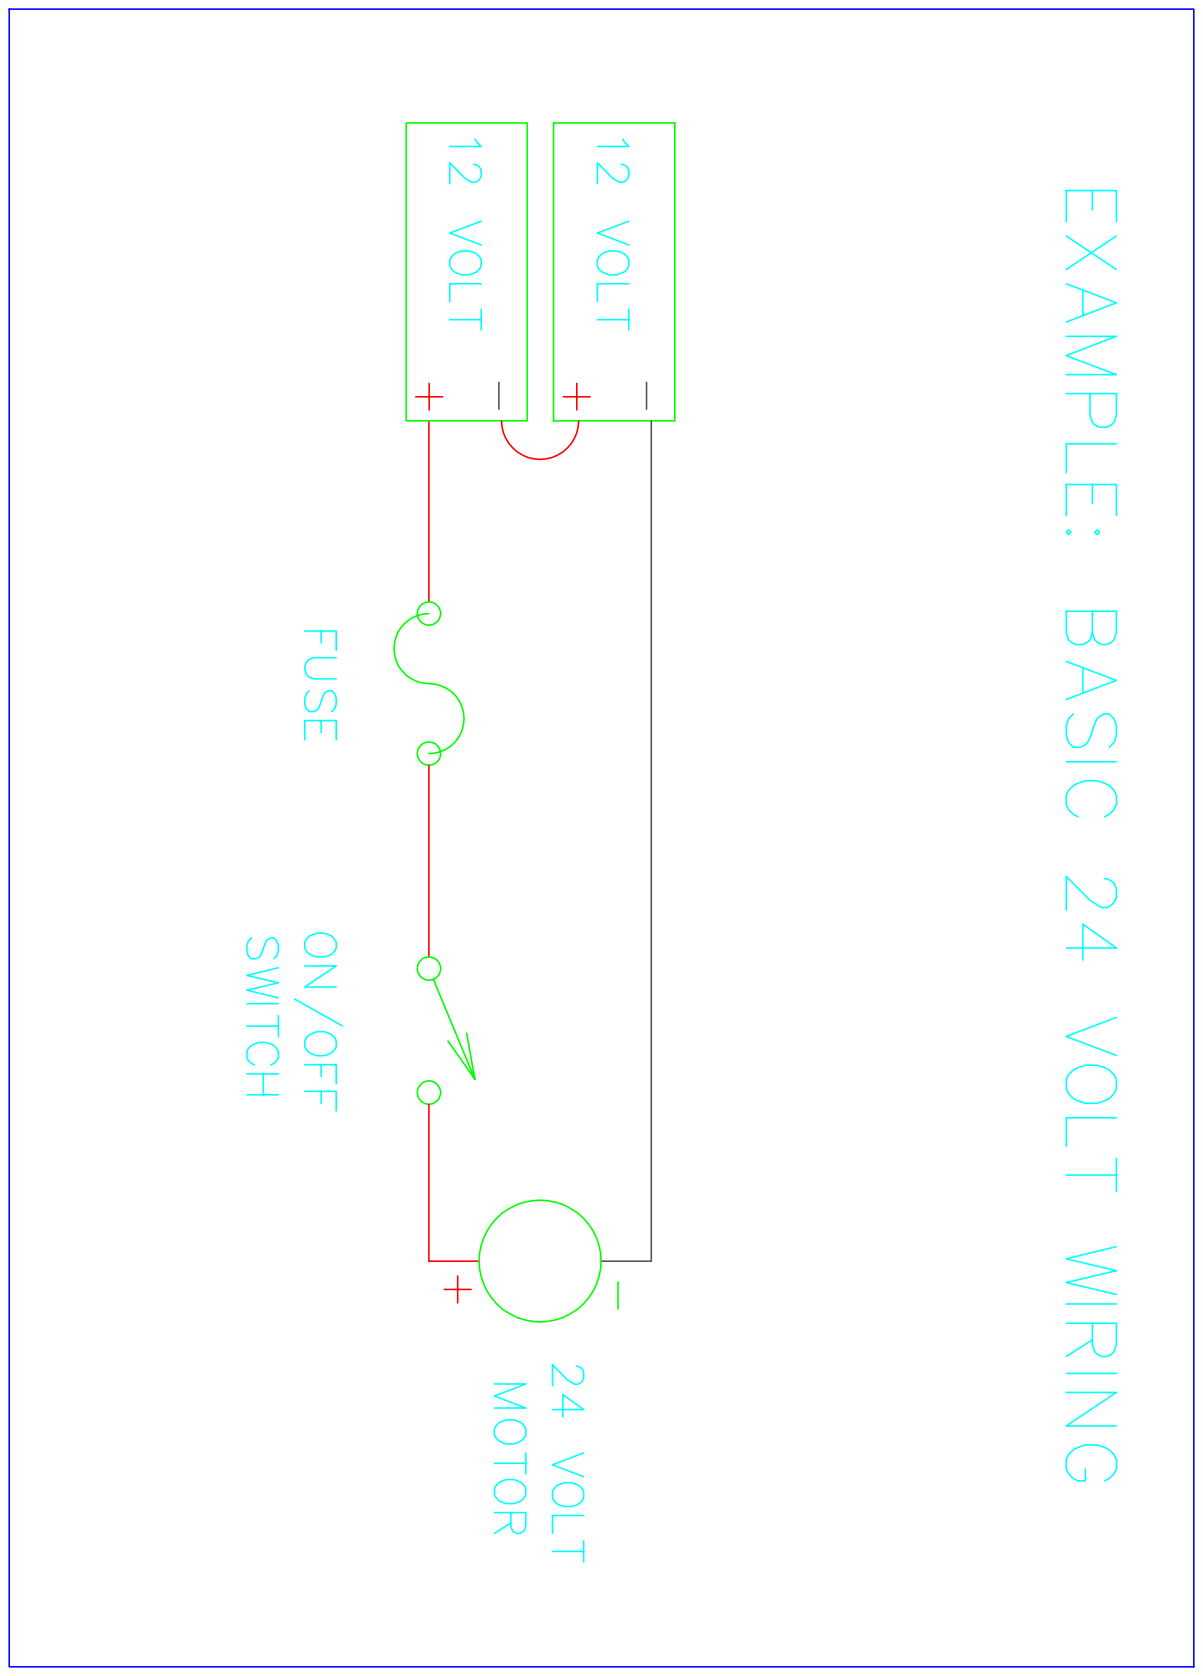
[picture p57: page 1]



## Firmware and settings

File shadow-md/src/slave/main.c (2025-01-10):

/*
 * 	main.c
 *  MarcDuino Slave (HoloProjector & Lights Control)
 *  Created on: July 4th, 2012
 *  Author: Marc Verdiell
 *  Version 1.2r: original release 03/26/2013
 *	Version 1.3r: adapting for new JEDI, McWhlr Magic Panel
 *	Version 1.4: consolidate private and release code, HP lights from MarcDuino, PassThrough command
 *	Version 1.5: new buffered serial
 *	Version 1.7: MarcDuino v2 support
 *  Version 1.8: I2C command parsing support, revised serial.c
 *
 */

/***********************
 *  Version 1.8:
 *  I2C command parsing support
 *  Updated serial.c and serial.h libraries
 *  	Changed serial_puts so it waits for available output buffer by default
 *  		If not characters were just dropped when sending data too fast.
 *  	Renamed previous version serial_puts_nowait
 *  Updated the comments in i2c.h
 *
 ***********************/

/**********
 * v1.7
 * MarcDuinoV2 support
 * 	Bumped to version 1.7 to match the Master release
 * 	New suart.c library with stuart2 on PC1 output instead of PC4
 * 	Exchange suart usage to macth MarcDuino v2 board (and Master)
 * 		- Light Output to suart2/PC1 (instead of suart)
 * 		- Slave output on suart/PC0 (instead of suart2)
 * 	I2C library support
 * 	REON holoprojector support
 */

/**********
 * v1.52
 * Added HP test movement command
 * Did not create new project
 */

/**********
 * v1.51
 * Corrected non centered HP servo, add extended movement option
 * (all done in the header files)
 * Did not create new project
 * Corrected debug message version
 */

/** v1.5
 *
 * Up'ed the version number to match the corresponding Dome Panel Control version
 * Switch to Interrupt Driven / Buffered serial implementation
 * Reduce delays after JEDI commands now that suart is more reliable
 */

/** v1.4
 * Add control of HP through our own board
 * 	ON and OF commands will turn on HPs located on srv7-9 headers
 * 	New HP lights commands
 * 	*H1xx, *H2xx, *H3xx, and *H0xx
 * 		Will turn on HP1, 2, 3, and all for xx seconds
 * 	*F1xx, *F2xx, *F3xx, and *F0xx
 * 		Will flicker HP1, 2, 3, and all for xx seconds
 * New library files:
 * 	RS232 with pgm memory for strings
 * 	Refactor sor serial calls
 * 	New realtime library with registered timers
 * 	Remove sequencer files
 *  Added print.c and print.h (convenience, adds 2% of code) (? do I need this)
 * Much smaller DRAM footprint for further expansino
 *  Change most strings constant to program memory strings
 * Support for Alt1 (!) and Alt2 (%) expansion commands
 * 	! commands output on suart (with strip)
 * 	% commands output on suart2 (with strip)
 * Disabled interrupts while transmitting in suart.h -> improved reliability
 */

/** v1.3
 *
 * Created compile switch for 9600 baud rate for new JEDI compatibility
 * Created compile switch for inverted on Magic Panel Output
 * 	(to works with my new Holo Lights and Michael Wheeler's magic panel)
 *
 */


/** Commands implemented in v1.2
 *
 * 	Hardware Setup:
 * 	- 6 servo outputs
 * 		Holo 1 V on pins 1 (front, holo 1)
 * 		Holo 1 H on pins 2
 * 		Holo 2 V on pins 3 (rear, holo 2)
 * 		Holo 2 H on pins 4
 * 		Holo 3 V on pins 5 (top, holo 3)
 * 		Holo 3 H on pins 6
 * 	- 4 digital outputs
 * 		HP1 (front, holo 1) on PORT B Pin 2 (pins labeled SRV7)
 * 		HP2 (rear, holo 2)  on PORT B Pin 3 (pins labeled SRV8)
 * 		HP3 (top, holo 3)   on PORT B Pin 4 (pins labeled SRV9)
 * 		Magic Panel on Port B Pin 5 (pins labeled SRV10)
 * 	- two suarts (software uart) output
 * 		- suart connected to the JEDI Display light control system at 2400 bauds
 * 		- suart2 initialized at 9600 bauds, for future use (daisy-chain expansion?)
 * 	- one RC input
 * 	- one main hardware UART input
 *		- connected to the master panel controller suart output at 9600 bauds, to receive commands
 *		- output sends commands acknowledgments, (not physically connected to anything at present)
 *
 *  Valid start characters recognized in main()
 *  ':' panel command, ignored (see parse_panel_command). This should not be received by this slaved module anyhow
 *  '$' sound command, ignored (see parse_sound_command). This should not be received by this slaved module anyhow
 *  '@' display command, forwarded to JEDI controller on suart1 after stripping the '@' control character
 *  '*' hp command, acted upon here, see below
 *  '!' Alt1 alternate display command, passed to suart after stripping
 *  '%' Alt2 expansion command, passed to suart2 after stripping
 *		The master HP board will forward these to us
 *
 *  Commands recognized (see parse_hp_command)
 *  *RDxx Random Holo movement (xx=01 to 03). xx=00 and >3 all random.
 *  *ONxx Turns Holo Light on (xx=01 to 03). xx=00 or >3 all lights on
 *  *OFxx Turns Holo Lights off (xx=01 to 03). xx=00 turns all lights off
 *  *RCxx Holo vertical movement under RC control, horizontal centered (xx=01-03).
 *  	00 or >3 all RC
 *  *TExx Holo movement test (xx=01-03). Goes through a loop of holo movements
 *  	to assist in adjusting holo servos mechanical setup
 *  	00 or >3 all HPs to test
 *  *STxx stop/reset Holos random movement, turns lights off, and RC off. 00=all off
 *  *HDxx hold: stop holo, do not change light level. 00=all stopped
 *  *MOxx magic panel on. xx=01 to 98, on from 1 to 98 seconds. 00=off, 99=on permanent
 *  *MFxx magic panel flicker xx=1 to 99 flicker for 1 to 99 seconds. 00= off.
 *  *H1xx, *H2xx, *H3xx, and *H0xx
 * 		Will turn on-board HP1, 2, 3, and all (HP0xx) for xx seconds
 * 		99 is on permanently.
 * 		0 is off.
 * 	*F1xx, *F2xx, *F3xx, and *F0xx
 * 		Will flicker on-board HP1, 2, 3, and all (F0xx) for xx seconds
 * 		0 is off.
 * 		(99 is not permanently, but 99 seconds)
 */

#include "main.h"

#include <util/delay.h>
#include <avr/io.h>
#include <avr/interrupt.h>  // needed for the UART interrupt
#include <avr/pgmspace.h>	// for the sequencer data arrays defined with PROGMEM

#include <stdlib.h>			// for itoa(), integer to string conversion
#include <errno.h>			// for errors on atoi (check errno)
#include <stdio.h>			// for sprintf(), don't use if you are short on memory
#include <string.h>			// for strlen()


#include "toolbox.h"		// map, digitalWrite, digitalMode
#include "servo.h"			// servo drivers
#include "realtime.h"		// real time interrupt services
#include "serial.h"			// hardware serial
#include "suart.h"			// software serial (write only)
#include "wmath.h"			// random functions
//#include "sequencer.h"		//  no servo sequencer
//#include "panel_sequences.h"	//  no panel sequences

#ifdef _MARCDUINOV2_
#include "i2c.h"			// include I2C Master libraries for MarcDuino v2
#endif

#define HP_NUM 3			// controlling 3 HPs for RC

// command globals
char command_buffer[CMD_MAX_LENGTH];	// command string buffer

 // Controls verbosity level - affecting i2c for now
 uint8_t errormessageon=_ERROR_MSG_;
 uint8_t feedbackmessageon=_FEEDBACK_MSG_;

// flags for the HP control mode (0=nothing, 1=random, 2=RC)
static uint8_t hp1_control=0;
static uint8_t hp2_control=0;
static uint8_t hp3_control=0;
// Magic panel and holo effect depends on the value of the following global flags:
// if it's 0, it's off
// if it's 1, it's on
// if it's 2, it's on as long as rt_timeout_magic_panel is non-zero
// if it's 3, random flicker as long as rt_timeout_magic_panel is non-zero
static uint8_t magic_control=0;
static uint8_t hp1_light_control=0;
static uint8_t hp2_light_control=0;
static uint8_t hp3_light_control=0;


// MarcDuino V2, holo states for I2C
// set them to 1 initially or they won't turn off during init...
uint8_t holo1state=1;
uint8_t holo2state=1;
uint8_t holo3state=1;

// timers

rt_timer move_timer_HP1;		// HP1 random movement timer
rt_timer move_timer_HP2;		// HP2 random movement timer
rt_timer move_timer_HP3;		// HP3 random movement timer

rt_timer on_timer_magic;		// magic on-time timer
rt_timer flicker_timer_magic;	// magic panel flicker timer

rt_timer on_timer_HP1;			// HP1 on-time timer
rt_timer on_timer_HP2;			// HP2 on-time timer
rt_timer on_timer_HP3;			// HP3 on-time timer
rt_timer flicker_timer_HP1; 	// HP1 flicker timer
rt_timer flicker_timer_HP2; 	// HP2 flicker timer
rt_timer flicker_timer_HP3; 	// HP3 flicker timer

rt_timer test_timer;			// For HP movement test

// string constants are in program memory to save DRAM
const char strOK[] PROGMEM="OK\n\r";
const char strWelcome[] PROGMEM="\n\rMarcDuino HP Control v1.52 \n\r";
const char strEnterPrompt[] PROGMEM="Enter HP or Display command starting with \'*\' or \'@\'\n\r";
const char strSuart1OK[] PROGMEM="\n\rsuart1 Communication OK \n\r";
const char strSuart2OK[] PROGMEM="\n\rsuart2 Communication OK \n\r";
const char strStartCharErr[] PROGMEM="**Unrecognized Command Start Character\r\n";

// utility to echo characters back cleanly
void echo(char ch)
{
	// echo return and line feeds nicely on a terminal
	if(ch=='\r' || ch=='\n' || ch == 0x0D )
	{
		serial_putc('\n');
		serial_putc('\r');
	}
	else serial_putc(ch);
}

int main(void) {

	// start hardware and software UARTs, send check string
	serial_init_9600b8N1();	// 9600 bauds, 8 bits, 1 stop, no parity, use for a regular terminal console
	serial_puts_p(strWelcome);
	serial_puts_p(strEnterPrompt);


// initialize suart used to communicate with the JEDI Display at 2400 or 9600 bauds
	uint16_t baudrate;
#ifdef _9600BAUDSJEDI_
	baudrate=9600;
#else
	baudrate=2400;
#endif
	lightsuart_init(baudrate);


	//suart_puts_p(strSuart1OK);
	//_delay_ms(200);

// suart used for slave out initialized at 9600 bauds, used for Alt2 commands
	slavesuart_init(9600);
#ifdef _MARCDUINOV2_
	slavesuart_puts_p(strSuart1OK); // on suart1 for MarcDuino v2
#else
	slavesuart_puts_p(strSuart2OK);	// on suart2 for MarcDuino v1
#endif


	// abort test routine, and optionally do extra Jedi programmatic setup
	_delay_ms(3000);		// wait that the display system is up
	init_jedi();

	// Received command characters from uart0 are processed asynchronously via interrupt handler
	// further below. They will be used to fill the 'command_buffer' string.
	// The 'command_buffer_full' flag will be raised when the full command is available.
	// The buffer is then read and processed in the main loop.
	serial_enable_rx_interrupt();

	// initialize servo and realtime units
	servo_init();
	realtime_init();

#ifdef _MARCDUINOV2_
	// initialize I2C hardware on MarcDuino v2's with 10k pull-up resistors on.
	i2c_init(TRUE);
#endif

	// register all our timers and timeouts

	rt_add_timer(&move_timer_HP1);
	rt_add_timer(&move_timer_HP2);
	rt_add_timer(&move_timer_HP3);
	rt_add_timer(&flicker_timer_magic);
	rt_add_timer(&on_timer_magic);
	rt_add_timer(&on_timer_HP1);
	rt_add_timer(&on_timer_HP2);
	rt_add_timer(&on_timer_HP3);
	rt_add_timer(&flicker_timer_HP1);
	rt_add_timer(&flicker_timer_HP2);
	rt_add_timer(&flicker_timer_HP3);
	rt_add_timer(&test_timer);

	// initialize magic panel and holo lights as output
	digitalMode(MAGIC_PORT, MAGIC_PIN, OUTPUT);
	digitalMode(HP1_LIGHT_PORT, HP1_LIGHT_PIN, OUTPUT);
	digitalMode(HP2_LIGHT_PORT, HP2_LIGHT_PIN, OUTPUT);
	digitalMode(HP3_LIGHT_PORT, HP3_LIGHT_PIN, OUTPUT);

	// turn off all lights
	holo1OFF();
	holo2OFF();
	holo3OFF();
	MAGIC_OFF;

  while (1)
  {
	/////////////////////////////////////////
	// Serial Command Input
	////////////////////////////////////////
	char command_str[CMD_MAX_LENGTH];
	bool command_available;

	// check for command line input
	if(serial_available())
	{
		char ch;
		ch=serial_getc();										// get input
		echo(ch);												// echo back
		command_available=build_command(ch, command_str);		// build command line
		if (command_available) dispatch_command(command_str);	// send command line to dispatcher
	}

	///////////////////////////////////////////
	// RC and random pattern of HP servos
	//////////////////////////////////////////

	 // How the servo is control depends on hpx_control flags
	 // if it's 0, nothing happens
	 // if it's 1, random pattern
	 // if it's 2, RC control of vertical servo

	 // *********  HP RC movement  ************************

	 if(hp1_control==2) {servo_set(FRONT_HP_SERVO_H, 1500); servo_set(FRONT_HP_SERVO_V, servo_RCread());}
	 if(hp2_control==2) {servo_set(REAR_HP_SERVO_H, 1500); servo_set(REAR_HP_SERVO_V, servo_RCread());}
	 if(hp3_control==2) {servo_set(TOP_HP_SERVO_H, 1500); servo_set(TOP_HP_SERVO_V, servo_RCread());}

	 // *********  HP random movement  ************************
	 if(hp1_control==1)
	 {
		 if(move_timer_HP1==0)
		 {
			 //move_timer_HP1 = rand_howsmall_howbig(50, 500);
			 move_timer_HP1 = rand_howsmall_howbig(20, 200);
			 servo_set(FRONT_HP_SERVO_H, rand_howsmall_howbig(SERVO_HP_MIN,SERVO_HP_MAX));
			 servo_set(FRONT_HP_SERVO_V, rand_howsmall_howbig(SERVO_HP_MIN,SERVO_HP_MAX));
		 }
	 }
	 if(hp2_control==1)
	 {
		 if(move_timer_HP2==0)
		 {
			 //move_timer_HP2 = rand_howsmall_howbig(50, 500);
			 move_timer_HP2 = rand_howsmall_howbig(20, 200);
			 servo_set(REAR_HP_SERVO_H, rand_howsmall_howbig(SERVO_HP_MIN,SERVO_HP_MAX));
			 servo_set(REAR_HP_SERVO_V, rand_howsmall_howbig(SERVO_HP_MIN,SERVO_HP_MAX));
		 }
	 }
	 if(hp3_control==1)
	 {
		 if(move_timer_HP3==0)
		 {
			 //move_timer_HP3 = rand_howsmall_howbig(50, 500);
			 move_timer_HP3 = rand_howsmall_howbig(20, 200);
			 servo_set(TOP_HP_SERVO_H, rand_howsmall_howbig(SERVO_HP_MIN,SERVO_HP_MAX));
			 servo_set(TOP_HP_SERVO_V, rand_howsmall_howbig(SERVO_HP_MIN,SERVO_HP_MAX));
		 }
	 }

	 // *********  HP test movement  ************************
	 // move servos to all extreme positions to adjust HP
	 if(hp1_control==3 || hp2_control==3 || hp3_control==3)
	 {
		 if(test_timer==0)
		 {
			 static uint8_t step;
			 static uint16_t a,b;
			 if (step>=17)step=0;
			 step ++;
			 test_timer = 200;
			 switch (step)
			 {
			 	 case 1: // center
			 		a=(SERVO_HP_MIN+SERVO_HP_MAX)/2;
			 		b=(SERVO_HP_MIN+SERVO_HP_MAX)/2;
			 		break;
			 	 case 2: // up
			 		a=(SERVO_HP_MIN+SERVO_HP_MAX)/2;
			 		b= SERVO_HP_MAX;
			 		break;
			 	 case 3: // center
			 		a=(SERVO_HP_MIN+SERVO_HP_MAX)/2;
			 		b=(SERVO_HP_MIN+SERVO_HP_MAX)/2;
			 		break;
			 	 case 4: // down
				 	a= (SERVO_HP_MIN+SERVO_HP_MAX)/2;
				 	b= SERVO_HP_MIN;
			 		break;
			 	 case 5: // center
			 		a=(SERVO_HP_MIN+SERVO_HP_MAX)/2;
			 		b=(SERVO_HP_MIN+SERVO_HP_MAX)/2;
			 		break;
			 	 case 6: // right
			 		a= SERVO_HP_MAX;
			 		b=(SERVO_HP_MIN+SERVO_HP_MAX)/2;
			 		break;
			 	 case 7: // center
			 		a=(SERVO_HP_MIN+SERVO_HP_MAX)/2;
			 		b=(SERVO_HP_MIN+SERVO_HP_MAX)/2;
			 		break;
			 	 case 8: // left
			 		a= SERVO_HP_MIN;
			 		b=(SERVO_HP_MIN+SERVO_HP_MAX)/2;
			 		break;
			 	 case 9: // center
			 		a=(SERVO_HP_MIN+SERVO_HP_MAX)/2;
			 		b=(SERVO_HP_MIN+SERVO_HP_MAX)/2;
			 		break;
			 	 case 10: // up/right
			 		a= SERVO_HP_MAX;
			 		b= SERVO_HP_MAX;
			 		break;
			 	 case 11: // center
			 		a=(SERVO_HP_MIN+SERVO_HP_MAX)/2;
			 		b=(SERVO_HP_MIN+SERVO_HP_MAX)/2;
			 		break;
			 	 case 12: // down/right
			 		a= SERVO_HP_MAX;
			 		b= SERVO_HP_MIN;
			 		break;
			 	 case 13: // center
			 		a=(SERVO_HP_MIN+SERVO_HP_MAX)/2;
			 		b=(SERVO_HP_MIN+SERVO_HP_MAX)/2;
			 		break;
			 	 case 14: // down/left
			 		a= SERVO_HP_MIN;
			 		b= SERVO_HP_MIN;
			 		break;
			 	 case 15: // center
			 		a=(SERVO_HP_MIN+SERVO_HP_MAX)/2;
			 		b=(SERVO_HP_MIN+SERVO_HP_MAX)/2;
			 		break;
			 	 case 16: // up/left
			 		a= SERVO_HP_MIN;
			 		b= SERVO_HP_MAX;
			 		break;
			 	 case 17: // center
			 		a=(SERVO_HP_MIN+SERVO_HP_MAX)/2;
			 		b=(SERVO_HP_MIN+SERVO_HP_MAX)/2;
			 		break;
			 	 default:
			 		 break;
			 }
			 if(hp1_control==3)
			 	 {servo_set(FRONT_HP_SERVO_H, a); servo_set(FRONT_HP_SERVO_V, b);}
			 if(hp2_control==3)
			 	 {servo_set(REAR_HP_SERVO_H, a); servo_set(REAR_HP_SERVO_V, b);}
			 if(hp3_control==3)
			 	 {servo_set(TOP_HP_SERVO_H, a); servo_set(TOP_HP_SERVO_V, b);}
		 }
	 }

	 ///////////////////////////////////////////////
	 // Magic panel control
	 //////////////////////////////////////////////

	 // Magic panel effect depends on the 'magic_control' flag:
	 // if it's 0, it's off
	 // if it's 1, it's on
	 // if it's 2, it's on as long as rt_timeout_magic_panel is non-zero
	 // if it's 3, random flicker as long as rt_timeout_magic_panel is non-zero

	 switch(magic_control)
	 {
	 	 case 0:
	 		 MAGIC_OFF;
	 		 break;
	 	 case 1:
	 		 MAGIC_ON;
	 		 break;
	 	 case 2:
	 		 if(on_timer_magic) MAGIC_ON;
	 		 else MAGIC_OFF;
	 		 break;
	 	 case 3:
	 		 if(!on_timer_magic) MAGIC_OFF;
	 		 else
	 		 {
	 			 if(!flicker_timer_magic)	// end of random flicker period
	 			 {
	 				// Michael Wheeler magic panel has reversed polarity
					#ifdef _REVERSEMAGICPANEL_
	 				if(!digitalRead(MAGIC_PORT,MAGIC_PIN)) // panel was on
					#else
	 				if(digitalRead(MAGIC_PORT,MAGIC_PIN)) // panel was on
					#endif
	 				{
	 					flicker_timer_magic=rand_howsmall_howbig(3,10);
	 					MAGIC_OFF;
	 				}
	 				else
	 				{
	 					flicker_timer_magic=rand_howsmall_howbig(5,20);
	 					MAGIC_ON;
	 				}
	 			 }
	 		 }
	 		 break;
	 	 default:
	 		 break;
	 }

	 ///////////////////////////////////////////////
	 // HP Light control
	 //////////////////////////////////////////////

	 // HP light mode depends on the 'hpx_light_control' flag:
	 // if it's 0, it's off
	 // if it's 1, it's on
	 // if it's 2, it's on as long as on_timer_HPx is non-zero
	 // if it's 3, random flicker as long as on_timer_HPx is non-zero


	 switch(hp1_light_control)
	 {
		 case 0:
			 holo1OFF();
			 break;
		 case 1:
			 holo1ON();
			 break;
		 case 2:
			 if(on_timer_HP1) holo1ON();
			 else holo1OFF();
			 break;
		 case 3:
			 if(!on_timer_HP1) holo1OFF();
			 else
			 {
				 if(!flicker_timer_HP1)	// end of random flicker period
				 {
					// check if panel was on
					#ifdef	_REVERSEHOLOS_
					if(!digitalRead(HP1_LIGHT_PORT,HP1_LIGHT_PIN))
					#else
					if(digitalRead(HP1_LIGHT_PORT,HP1_LIGHT_PIN))
					#endif
					{
						flicker_timer_HP1=rand_howsmall_howbig(3,10);
						holo1OFF();
					}
					else
					{
						flicker_timer_HP1=rand_howsmall_howbig(5,20);
						holo1WHITE();
					}
				 }
			 }
			 break;
		 default:
			 break;
	 }

	 switch(hp2_light_control)
	 {
		 case 0:
			 holo2OFF();
			 break;
		 case 1:
			 holo2ON();
			 break;
		 case 2:
			 if(on_timer_HP2) holo2ON();
			 else holo2OFF();
			 break;
		 case 3:
			 if(!on_timer_HP2) holo2OFF();
			 else
			 {
				 if(!flicker_timer_HP2)	// end of random flicker period
				 {
					// check if panel was on
					#ifdef	_REVERSEHOLOS_
					if(!digitalRead(HP2_LIGHT_PORT,HP2_LIGHT_PIN))
					#else
					if(digitalRead(HP2_LIGHT_PORT,HP2_LIGHT_PIN))
					#endif
					{
						flicker_timer_HP2=rand_howsmall_howbig(3,10);
						holo2OFF();
					}
					else
					{
						flicker_timer_HP2=rand_howsmall_howbig(5,20);
						holo2WHITE();
					}
				 }
			 }
			 break;
		 default:
			 break;
	 }

	 switch(hp3_light_control)
	 {
		 case 0:
			 holo3OFF();
			 break;
		 case 1:
			 holo3ON();
			 break;
		 case 2:
			 if(on_timer_HP3) holo3ON();
			 else holo3OFF();
			 break;
		 case 3:
			 if(!on_timer_HP3) holo3OFF();
			 else
			 {
				 if(!flicker_timer_HP3)	// end of random flicker period
				 {
					// check if panel was on
					#ifdef	_REVERSEHOLOS_
					if(!digitalRead(HP3_LIGHT_PORT,HP3_LIGHT_PIN))
					#else
					if(digitalRead(HP3_LIGHT_PORT,HP3_LIGHT_PIN))
					#endif
					{
						flicker_timer_HP3=rand_howsmall_howbig(3,10);
						holo3OFF();
					}
					else
					{
						flicker_timer_HP3=rand_howsmall_howbig(5,20);
						holo3WHITE();
					}
				 }
			 }
			 break;
		 default:
			 break;
	 }

	/***** simple debug RC input test: loopback input to servo */
	//servo_set(2, servo_RCread());

	/***** simple input RC diagnostic test: prints out the RC input value
	char string[17]; 				// put outside while loop?
	sprintf(string, "RC-in: %04d \r\n", servo_RCread());
	serial_puts(string);
	*/

  }
return 0;
}

// builds the command string from the character input
uint8_t build_command(char ch, char* output_str)
{
	static uint8_t pos=0;

	switch(ch)
	{
		case CMD_END_CHAR:								// end character recognized
			command_buffer[pos]='\0';					// append the end of string character
			pos=0;										// reset buffer pointer
			strcpy(output_str, (char*)command_buffer);	// copy result
			return TRUE;								// return and signal command ready
			break;

		default:										// regular character
			command_buffer[pos]=ch;						// append the  character to the command string
			if(pos<=CMD_MAX_LENGTH-1)pos++;				// too many characters, discard them.
			break;
	}
	return FALSE;
}

// dispatches further command processing depending on start character
void dispatch_command(char* command_str)
{
	char start_char=command_str[0];
	uint8_t length=strlen(command_str);

	// prompt on empty command to show life at console
	if(length==0)
	{
		serial_puts_p(strOK);
		return;
	}

	// dispatch the command to the appropriate parser depending on start character
	switch(start_char)
	{
	 case PANEL_START_CHAR:
		 parse_panel_command(command_str, length);
		 break;
	 case HP_START_CHAR:
		 parse_hp_command(command_str, length);
		 break;
	 case DISPLAY_START_CHAR:
		 parse_display_command(command_str,length);
		 break;
	 case SOUND_START_CHAR:
		parse_sound_command(command_str,length);
		break;
	 case ALT1_START_CHAR:
		parse_alt1_command(command_str,length);
		break;
	 case ALT2_START_CHAR:
		parse_alt2_command(command_str,length);
		break;
	 case I2C_START_CHAR:
		 parse_i2c_command(command_str,length);
		 break;
	 default:
		 if(errormessageon) serial_puts_p(strStartCharErr);
		 break;
	}
}


const char strPanelCommandIgnored[] PROGMEM="Panel command - ignored\r\n";
void parse_panel_command(char* command, uint8_t length)
{
	// we should not receive any of this, ignore
	if(feedbackmessageon) serial_puts_p(strPanelCommandIgnored);
}
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

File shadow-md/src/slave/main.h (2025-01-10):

/*
 * main.h
 * 	MarcDuino Slave HP control
 * 	Author: Marc Verdiell
 * 	v1.8
 *
 * 	See description in implementation file
 *
 */

#ifndef MAIN_H_
#define MAIN_H_

#include <stdint.h> 		// uint8_t and companions

/********* BUILD SETTINGS FOR ALL VARIANTS, COMMENT IN OR OUT TO CHANGE OPTIONS ********/
#define _RELEASEVERSION_		// un-comment for public release
#define _MARCDUINOV2_			// for the V2 boards
/***************************************************************************************/

// turn to 1 for debug only
#define _ERROR_MSG_ 1
#define _FEEDBACK_MSG_ 1

// default to private version settings
#ifndef _RELEASEVERSION_
#define _PRIVATEVERSION_		// settings for my own droid
#endif


// settings for the public release version are here
#ifdef _RELEASEVERSION_
	#define _REVERSEMAGICPANEL_				// for compatibility with Michael Wheeler's Magic Panel and my own Holo Lights
	#define _REVERSEHOLOS_					// my own HoloLights 2.0 are easier to connect using the reverse logic also
	//#define _9600BAUDSJEDI_				// for compatibility with future version of JEDI display
	//#define _RESTRICT_HP_SERVO_RANGE_		// you could turn that one on if your HP servos move to much and go to end of travel
	//#define _EXTEND_HP_SERVO_RANGE_		// For Jason and the users of the BobC holo kit
#endif

// settings for my own droid version are here
#ifdef _PRIVATEVERSION_
	#define _DIGITALJEDI_					// my JEDI setting is non-standard
//	#define	_REVERSEMAGICPANEL_				// my own magic panel works opposite from Michael Weir's and my own Holo Lights
//	#define _REVERSEHOLOS_					// ### while debugging with v2.0 holo lights
	#define _RESTRICT_HP_SERVO_RANGE_		// smaller range of servo movement to fit my HP setup
//	#define _9600BAUDSJEDI_					// for future compatibility with new version of JEDI display

#endif

#define CMD_MAX_LENGTH   64		//Max length of the command string

// all commands must start with one of these characters
#define PANEL_START_CHAR 	':'
#define HP_START_CHAR		'*'
#define DISPLAY_START_CHAR 	'@'
#define SOUND_START_CHAR 	'$'
#define ALT1_START_CHAR		'!'	// for custom extensions, messages get forwarded on SUART (PC0) pin of slave HPPanel Marcduino
#define ALT2_START_CHAR		'%'	// for custom extensions, messages get forwarded on SUART2(PC4) pin of slave HPPanel Marcduino
#define I2C_START_CHAR		'&' // for outputting an i2c commands

// all command must end with one of these characters
#define CMD_END_CHAR 	'\r'

// I2C control characters (not used, hard coded for now)
#define CMD_SEP_CHAR	','		// separator for I2C arguments
#define CMD_HEX_CHAR	'x' 	// for hex numbers
#define CMD_CHAR_CHAR	'\'' 	// char delimiter
#define CMD_STR_CHAR	'"' 	// string delimiter

// define HP servo max random movement, and which servo positions are they connected to
#ifdef _RESTRICT_HP_SERVO_RANGE_
	#define SERVO_HP_MIN 		1200		// constrains the holo servo max swing
	#define SERVO_HP_MAX 		1800	// in both axis (usual RC min is 1000 and max is 2000)
#elif  defined(_EXTEND_HP_SERVO_RANGE_)
	#define SERVO_HP_MIN 		600		// constrains the holo servo extreme positions
	#define SERVO_HP_MAX 		2400	// in both axis (usual RC min is 500 and max is 2000)
#else
	#define SERVO_HP_MIN 		1000	// constrains the holo servo extreme positions
	#define SERVO_HP_MAX 		2000	// in both axis (version 1.5 had 500 as min, in error)
#endif

#define FRONT_HP_SERVO_H 	1
#define FRONT_HP_SERVO_V 	2
#define REAR_HP_SERVO_H 	3
#define REAR_HP_SERVO_V 	4
#define TOP_HP_SERVO_H 		5
#define TOP_HP_SERVO_V 		6

// define magic panel connection (was servo 10)
#define MAGIC_PORT	PORTB
#define MAGIC_PIN	5

// define holo Lights connection (was servo 10)
#define HP1_LIGHT_PORT	PORTB	// front
#define HP1_LIGHT_PIN	2
#define HP2_LIGHT_PORT	PORTB	// rear
#define HP2_LIGHT_PIN	3
#define HP3_LIGHT_PORT	PORTB	// top
#define HP3_LIGHT_PIN	4

#ifdef _REVERSEHOLOS_	//inverted logic, low is on
#define HP1_ON digitalWrite(HP1_LIGHT_PORT, HP1_LIGHT_PIN, LOW)
#define HP1_OFF digitalWrite(HP1_LIGHT_PORT, HP1_LIGHT_PIN, HIGH)
#define HP2_ON digitalWrite(HP2_LIGHT_PORT, HP2_LIGHT_PIN, LOW)
#define HP2_OFF digitalWrite(HP2_LIGHT_PORT, HP2_LIGHT_PIN, HIGH)
#define HP3_ON digitalWrite(HP3_LIGHT_PORT, HP3_LIGHT_PIN, LOW)
#define HP3_OFF digitalWrite(HP3_LIGHT_PORT, HP3_LIGHT_PIN, HIGH)
#else					// positive logic, high is on
#define HP1_ON digitalWrite(HP1_LIGHT_PORT, HP1_LIGHT_PIN, HIGH)
#define HP1_OFF digitalWrite(HP1_LIGHT_PORT, HP1_LIGHT_PIN, LOW)
#define HP2_ON digitalWrite(HP2_LIGHT_PORT, HP2_LIGHT_PIN, HIGH)
#define HP2_OFF digitalWrite(HP2_LIGHT_PORT, HP2_LIGHT_PIN, LOW)
#define HP3_ON digitalWrite(HP3_LIGHT_PORT, HP3_LIGHT_PIN, HIGH)
#define HP3_OFF digitalWrite(HP3_LIGHT_PORT, HP3_LIGHT_PIN, LOW)
#endif
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

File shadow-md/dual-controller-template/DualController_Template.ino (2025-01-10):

// =======================================================================================
//        SHADOW_MD:  Small Handheld Arduino Droid Operating Wand + MarcDuino
// =======================================================================================
//                          Last Revised Date: 08/23/2015
//                             Revised By: vint43
//                Inspired by the PADAWAN / KnightShade SHADOW effort
// =======================================================================================
//
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
//         This program is distributed in the hope that it will be useful 
//         as a courtesy to fellow astromech club members wanting to develop
//         their own droid control system.
//
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
//         You are using this software at your own risk and, as a fellow club member, it is
//         expected you will have the proper experience / background to handle and manage that 
//         risk appropriately.  It is completely up to you to insure the safe operation of
//         your droid and to validate and test all aspects of your droid control system.
//
// =======================================================================================
//   Note: You will need a Arduino Mega ADK rev3 to run this sketch,
//   as a normal Arduino (Uno, Duemilanove etc.) doesn't have enough SRAM and FLASH
//
//   This is written to be a SPECIFIC Sketch - supporting only one type of controller
//      - PS3 Move Navigation + MarcDuino Dome Controller & Optional Body Panel Controller
//
//   PS3 Bluetooth library - developed by Kristian Lauszus (kristianl@tkjelectronics.com)
//   For more information visit my blog: http://blog.tkjelectronics.dk/ or
//
//   Sabertooth (Foot Drive):
//         Set Sabertooth 2x32 or 2x25 Dip Switches: 1 and 2 Down, All Others Up
//
//   SyRen 10 Dome Drive:
//         For SyRen packetized Serial Set Switches: 1, 2 and 4 Down, All Others Up
//         NOTE:  Support for SyRen Simple Serial has been removed, due to problems.
//         Please contact DimensionEngineering to get an RMA to flash your firmware
//         Some place a 10K ohm resistor between S1 & GND on the SyRen 10 itself
//
// =======================================================================================
//
// ---------------------------------------------------------------------------------------
//                        General User Settings
// ---------------------------------------------------------------------------------------

String PS3ControllerFootMac = "XX:XX:XX:XX:XX:XX";  //Set this to your FOOT PS3 controller MAC address
String PS3ControllerDomeMAC = "XX:XX:XX:XX:XX:XX";  //Set to a secondary DOME PS3 controller MAC address (Optional)

String PS3ControllerBackupFootMac = "XX";  //Set to the MAC Address of your BACKUP FOOT controller (Optional)
String PS3ControllerBackupDomeMAC = "XX";  //Set to the MAC Address of your BACKUP DOME controller (Optional)

byte drivespeed1 = 70;   //For Speed Setting (Normal): set this to whatever speeds works for you. 0-stop, 127-full speed.
byte drivespeed2 = 110;  //For Speed Setting (Over Throttle): set this for when needing extra power. 0-stop, 127-full speed.

byte turnspeed = 50;      // the higher this number the faster it will spin in place, lower - the easier to control.
                         // Recommend beginner: 40 to 50, experienced: 50+, I like 75

byte domespeed = 100;    // If using a speed controller for the dome, sets the top speed
                         // Use a number up to 127

byte ramping = 1;        // Ramping- the lower this number the longer R2 will take to speedup or slow down,
                         // change this by increments of 1

byte joystickFootDeadZoneRange = 15;  // For controllers that centering problems, use the lowest number with no drift
byte joystickDomeDeadZoneRange = 10;  // For controllers that centering problems, use the lowest number with no drift

byte driveDeadBandRange = 10;     // Used to set the Sabertooth DeadZone for foot motors

int invertTurnDirection = -1;   //This may need to be set to 1 for some configurations

byte domeAutoSpeed = 70;     // Speed used when dome automation is active - Valid Values: 50 - 100
int time360DomeTurn = 2500;  // milliseconds for dome to complete 360 turn at domeAutoSpeed - Valid Values: 2000 - 8000 (2000 = 2 seconds)

#define SHADOW_DEBUG       //uncomment this for console DEBUG output
#define SHADOW_VERBOSE     //uncomment this for console VERBOSE output
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

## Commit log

2024-12-29 Fix: c_cpp_properties file mac Framework path
2025-01-10 add ref material to project
    [ANH-skins_1.dxf, Ankle Bottom Plate.dxf, Ankle Bracelet Front.dxf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]

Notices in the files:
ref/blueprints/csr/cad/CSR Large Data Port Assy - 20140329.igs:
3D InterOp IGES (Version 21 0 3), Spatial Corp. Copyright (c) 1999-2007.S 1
